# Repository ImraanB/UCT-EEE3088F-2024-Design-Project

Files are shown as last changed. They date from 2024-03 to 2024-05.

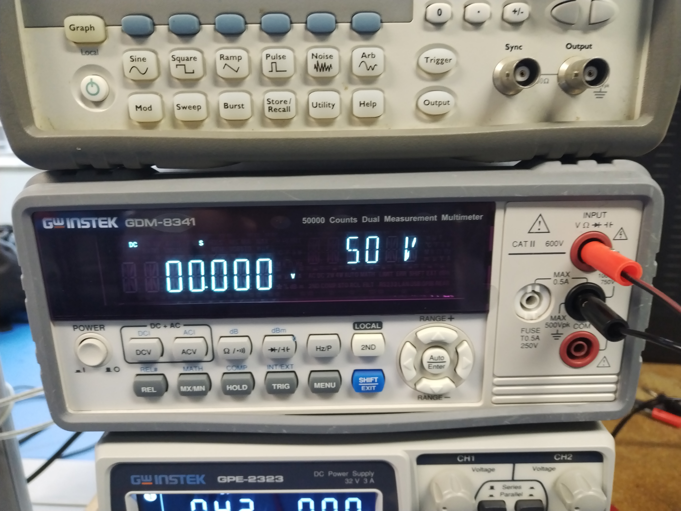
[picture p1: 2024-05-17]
Power subsystem/Testing/Testing pictures/IMG_20240510_095945.jpg

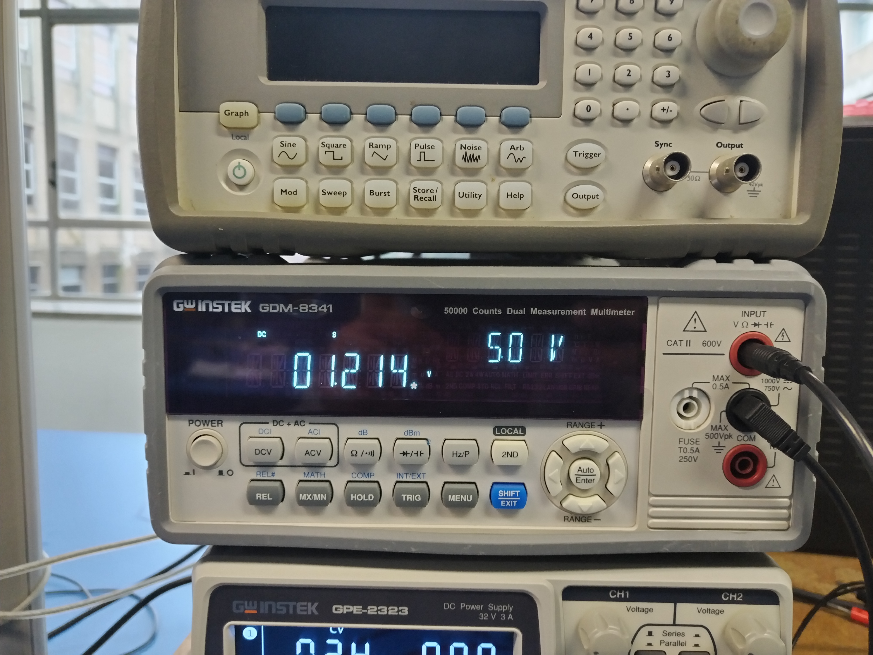
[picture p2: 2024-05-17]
Power subsystem/Testing/Testing pictures/adc voltage at 2v4.jpg

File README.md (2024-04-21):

# UCT-EEE3088F-2024-Design-Project
This is a repository for the UCT EEE3088F 2024 Micro-mouse Project
# Overall Project
This project involves designing a micromouse that will be able to move through a maze.
There are 4 subsystems that work together to form the micromouse:
## The motherboard
(We are given this) Connects all the PCBs together.
## The Processor
(We are given this) Contains an STM32L476 microcontroller. This microcontroller will be used to program different sections and subsystems of the micromouse.
## The Power
Responsible for powering the entire system:
- Run motors and charge battery
- Fit onto pin headers on motherboard
- It will need to be able to be an apporpriate size for balance and space issues
## The Sensor
Resposible for detecting/sensing objects
- Detect objects
- Fit onto pin headers on motherboard
- It will need to be able to be an apporpriate size for balance and space issues

# How this GitHub repo works
There are 2 main folders for the 2 subsystems that need to be designed: Power and Sensing.
Each of these folders contain the relevant documents that are associated with each subsystem

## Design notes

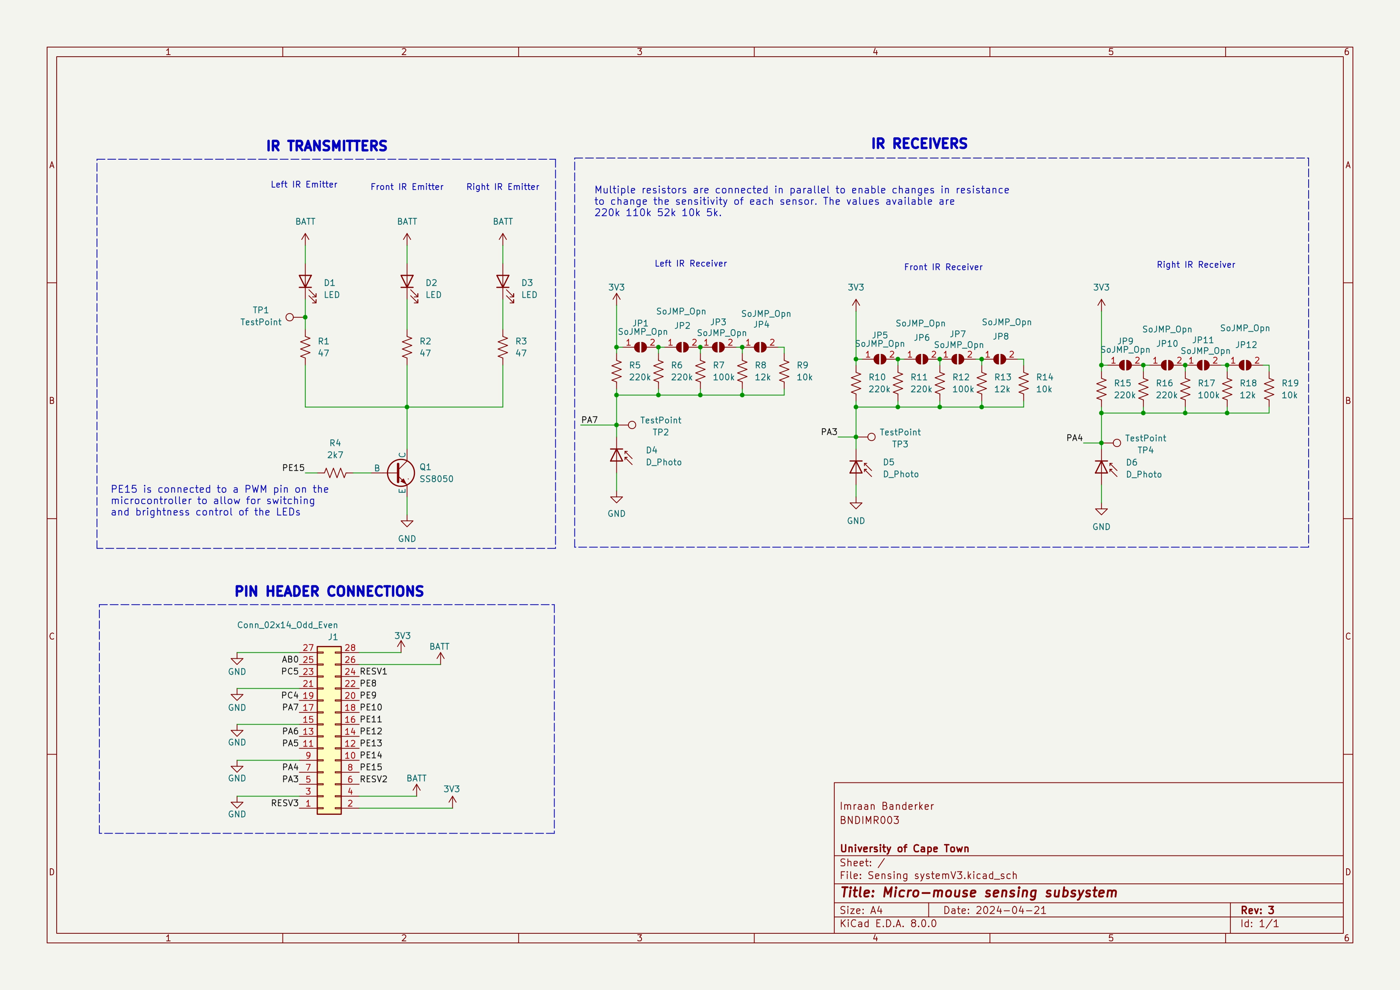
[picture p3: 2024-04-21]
Sensing subsystem/Images/Final Schematic.jpg

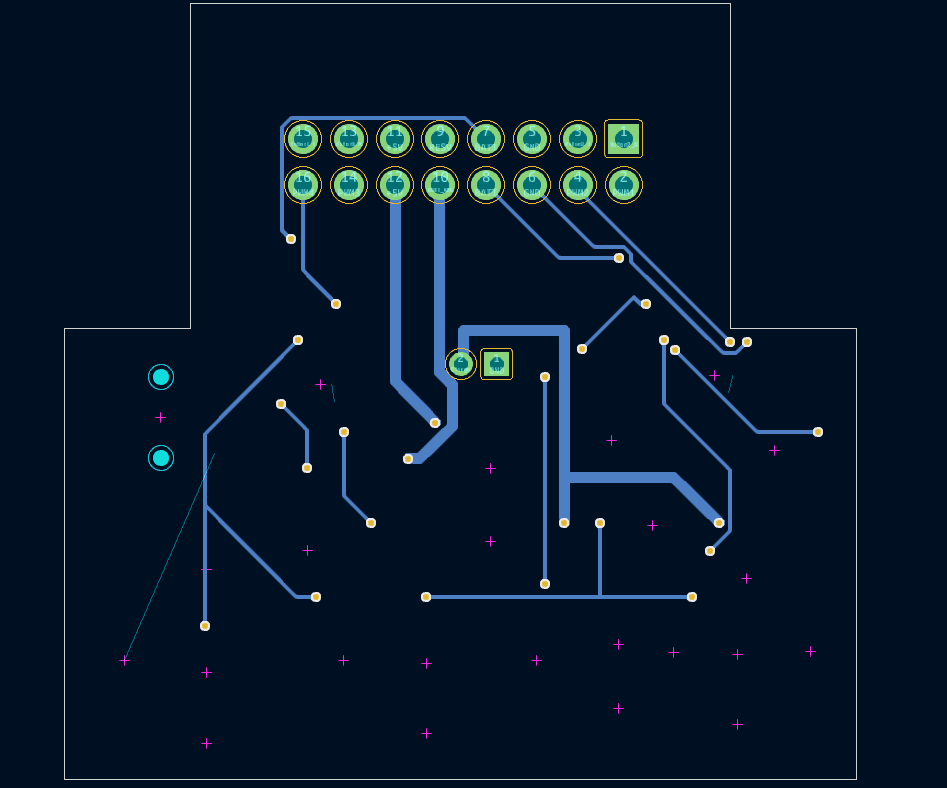
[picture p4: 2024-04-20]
Power subsystem/Design plan/Back PCB.png

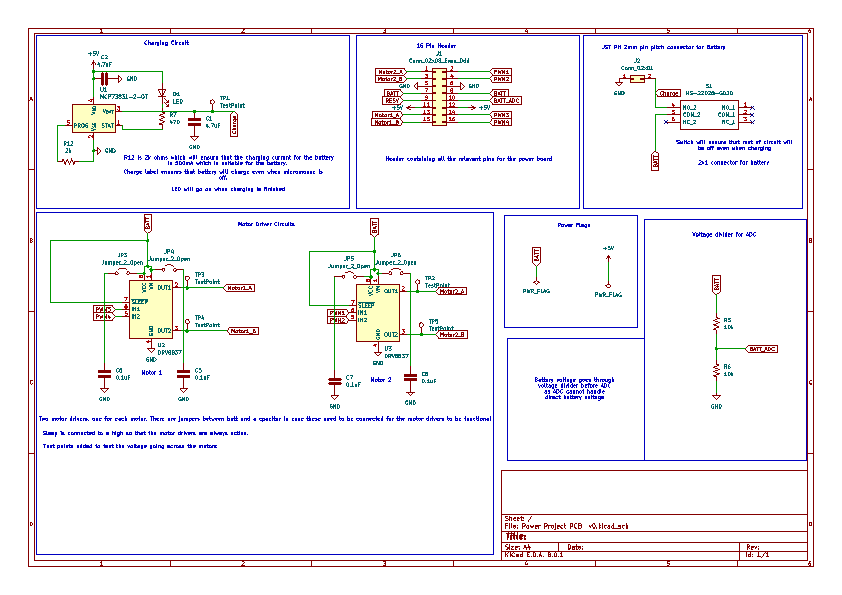
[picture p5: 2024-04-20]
Power subsystem/Design plan/Final Schematic.png

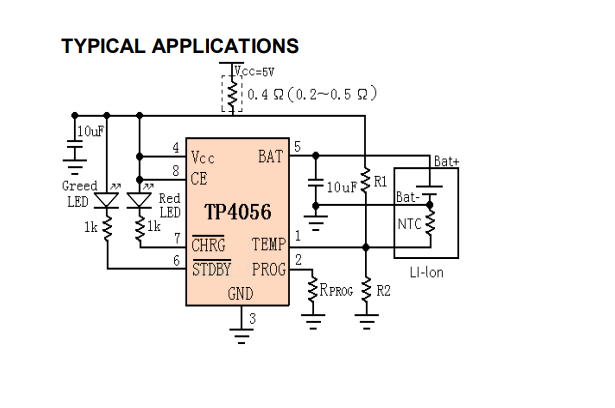
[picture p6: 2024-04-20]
Power subsystem/Design plan/TP4056 charging circuit.png

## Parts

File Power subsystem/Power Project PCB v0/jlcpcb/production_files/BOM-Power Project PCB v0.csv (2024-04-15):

Comment | Designator | Footprint | LCSC
10k | R5,R6 | R_0805_2012Metric | C17414
2k | R12 | R_0805_2012Metric | C17604
470 | R7 | R_0805_2012Metric | C17710
4.7uF | C1,C2,C5,C6,C7,C8 | C_0805_2012Metric | C1779
DRV8837 | U2,U3 | WSON-8-1EP_2x2mm_P0.5mm_EP0.9x1.6mm | C39159
MCP73831-2-OT | U1 | SOT-23-5 | C424093
LED | D1 | LED_0805_2012Metric | C84256
MS-22D28-G020 | S1 | MS22D28G020 | C963205

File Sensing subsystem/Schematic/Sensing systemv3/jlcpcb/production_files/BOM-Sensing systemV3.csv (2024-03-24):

Comment | Designator | Footprint | LCSC
100k | R12,R17,R7 | R_0805_2012Metric | C149504
10k | R14,R19,R9 | R_0805_2012Metric | C17414
12k | R13,R18,R8 | R_0805_2012Metric | C17444
2k7 | R4 | R_0805_2012Metric | C17530
220k | R10,R11,R15,R16,R5,R6 | R_0805_2012Metric | C17556
47 | R1,R2,R3 | R_0805_2012Metric | C17714
SS8050 | Q1 | SOT-23-3 | C2150
LED | D1,D2,D3 | LED_D5.0mm_Horizontal_O1.27mm_Z3.0mm_Clear | C405270
D_Photo | D4,D5,D6 | LED_D5.0mm_Horizontal_O1.27mm_Z3.0mm_Clear | C95399

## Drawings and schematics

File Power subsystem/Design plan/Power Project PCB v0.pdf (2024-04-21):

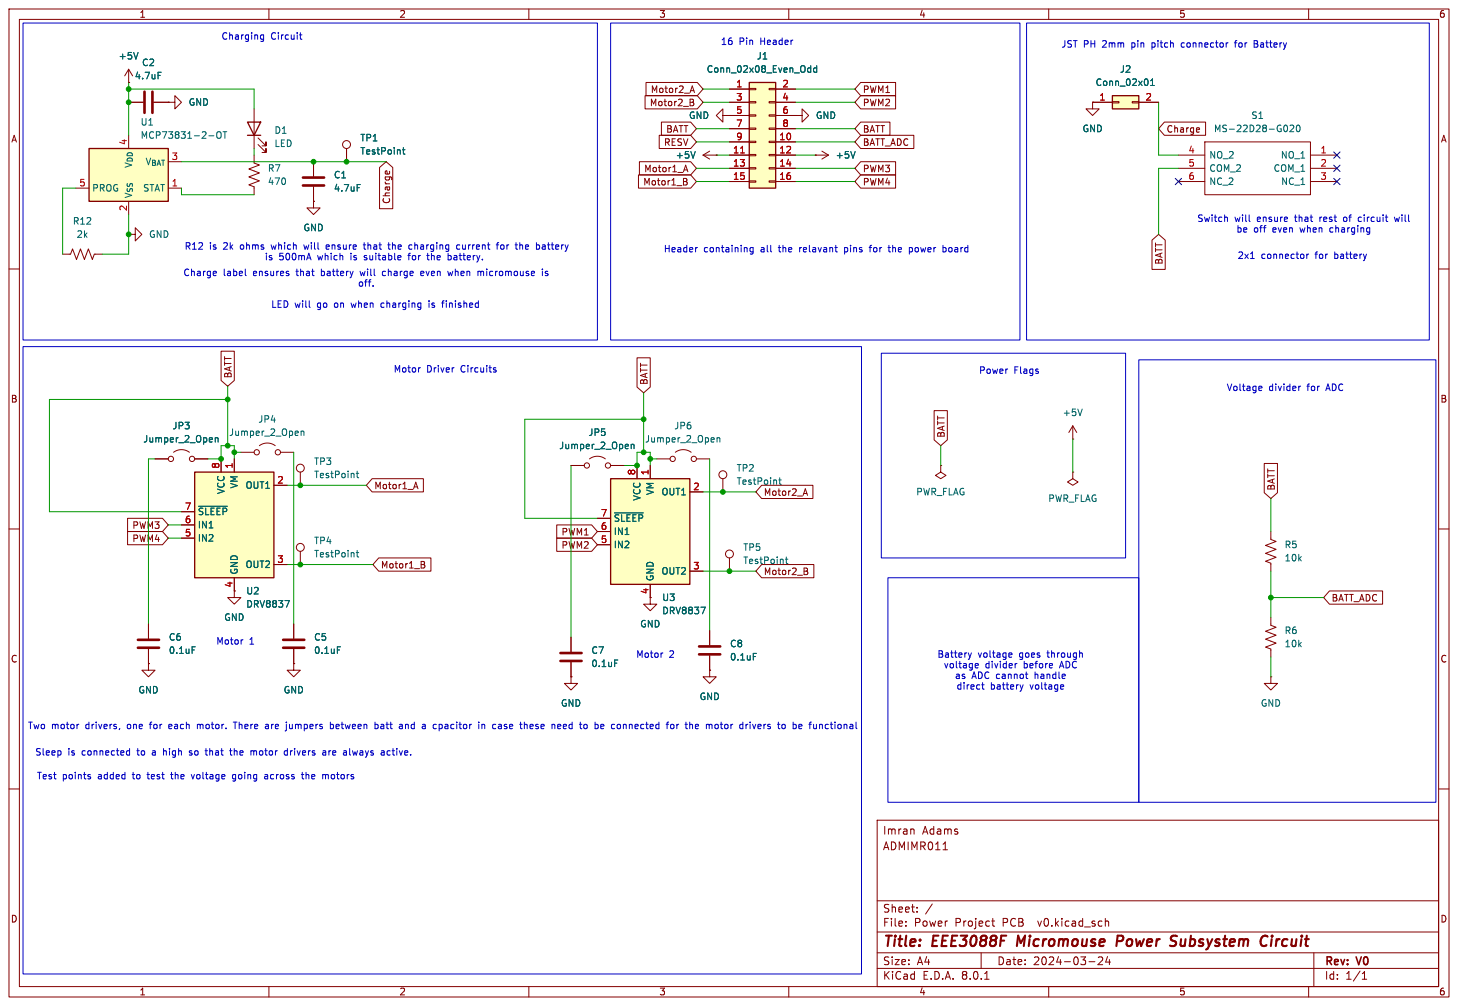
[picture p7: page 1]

Voltage divider for ADC

voltage divider before ADC
as ADC cannot handle

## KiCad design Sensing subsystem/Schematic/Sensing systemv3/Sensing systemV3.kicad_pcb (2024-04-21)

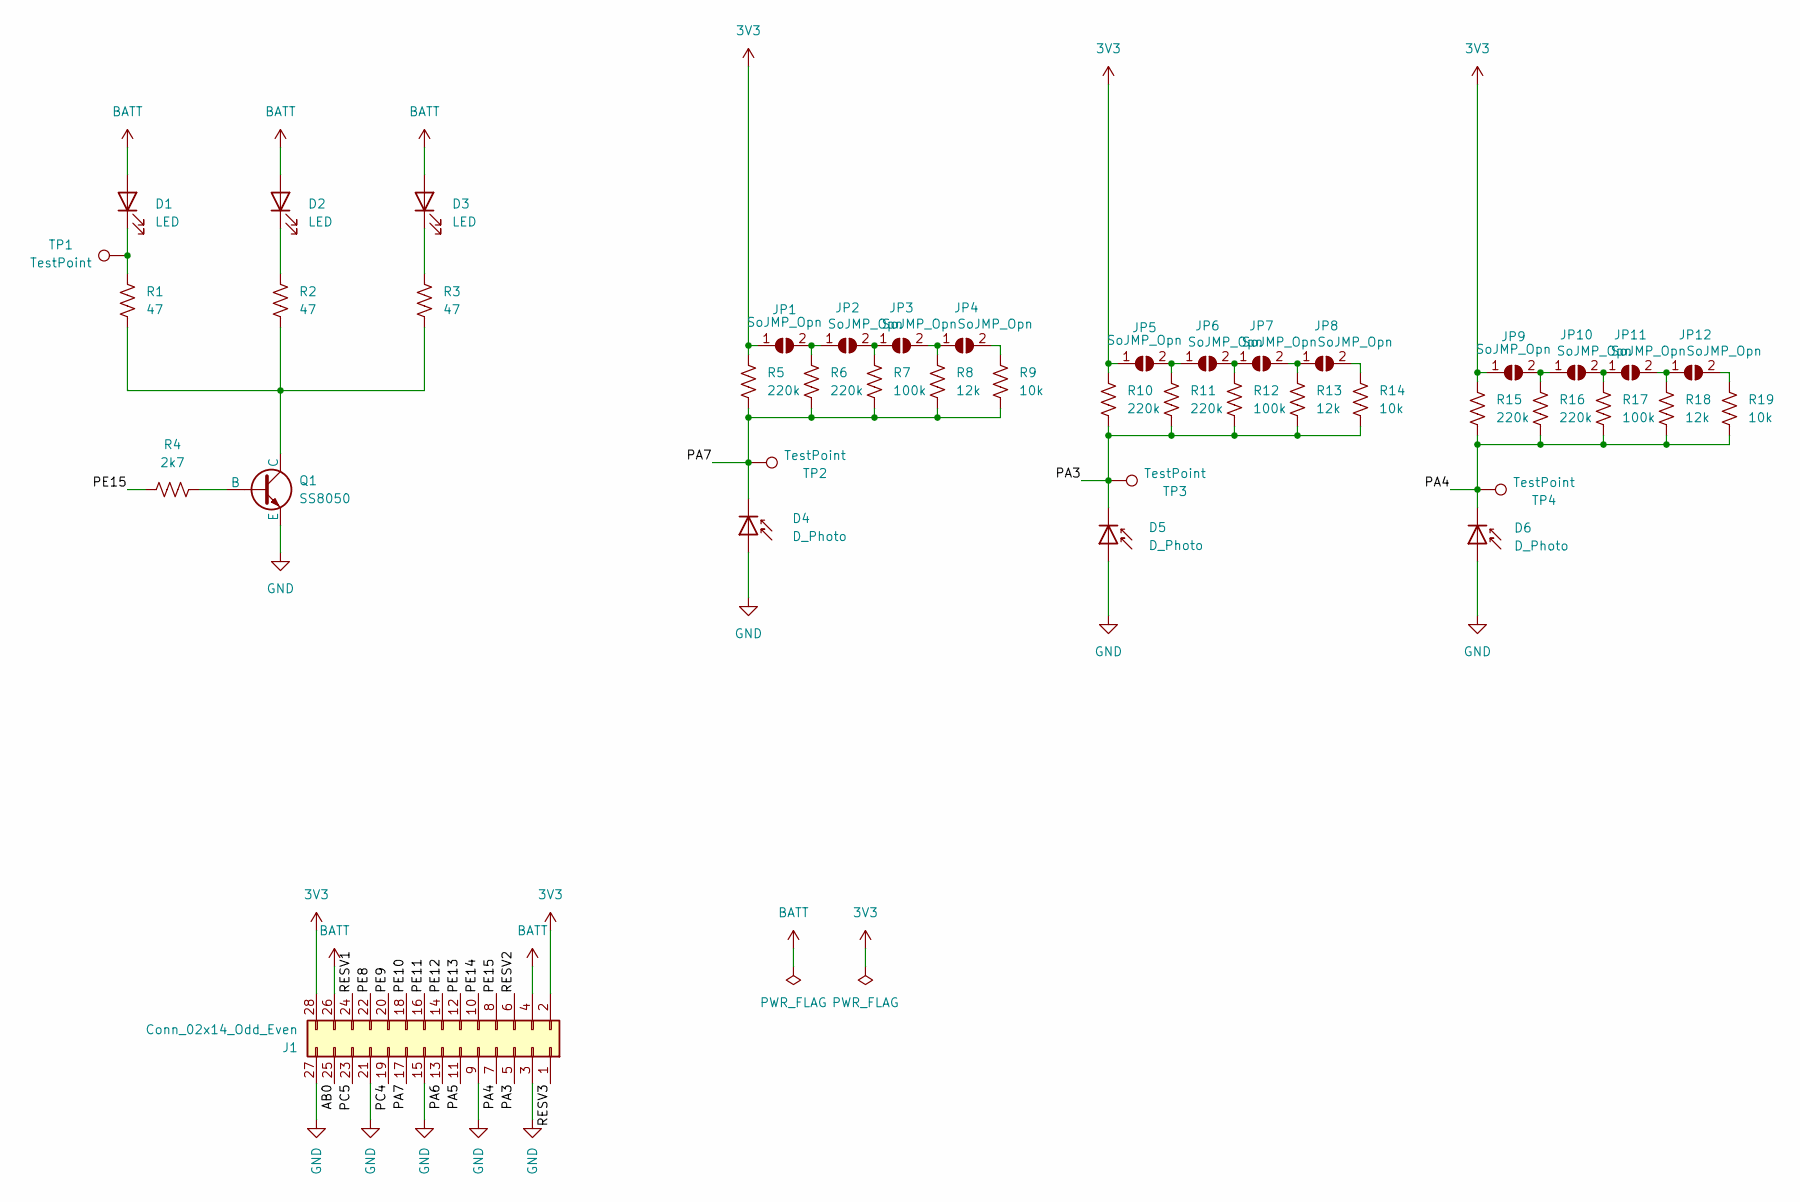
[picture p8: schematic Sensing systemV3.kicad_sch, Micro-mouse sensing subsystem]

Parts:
D1, D2, D3: LED; LED_D5.0mm_Horizontal_O1.27mm_Z3.0mm_Clear; LCSC C405270
D4, D5, D6: D_Photo; LED_D5.0mm_Horizontal_O1.27mm_Z3.0mm_Clear; LCSC C95399
J1: Conn_02x14_Odd_Even; PinHeader_2x14_P2.54mm_Vertical
JP1, JP2, JP3, JP4, JP5, JP6, JP7, JP8, JP9, JP10, JP11, JP12: SoJMP_Opn; SolderJumper-2_P1.3mm_Open_RoundedPad1.0x1.5mm
Q1: SS8050; SOT-23-3; LCSC C2150
R1, R2, R3: 47; R_0805_2012Metric; LCSC C17714
R4: 2k7; R_0805_2012Metric; LCSC C17530
R5, R6, R10, R11, R15, R16: 220k; R_0805_2012Metric; LCSC C17556
R7, R12, R17: 100k; R_0805_2012Metric; LCSC C149504
R8, R13, R18: 12k; R_0805_2012Metric; LCSC C17444
R9, R14, R19: 10k; R_0805_2012Metric; LCSC C17414
TP1, TP2, TP3, TP4: TestPoint; TestPoint_Pad_2.0x2.0mm

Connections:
3V3: J1.2, J1.28, JP1.1 (A), JP5.1 (A), JP9.1 (A), R5.1, R10.1, R15.1
/AB0: J1.25
/PA3: D5.1 (K), J1.5, R10.2, R11.2, R12.2, R13.2, R14.2, TP3.1
/PA4: D6.1 (K), J1.7, R15.2, R16.2, R17.2, R18.2, R19.2, TP4.1
/PA5: J1.11
/PA6: J1.13
/PA7: D4.1 (K), J1.17, R5.2, R6.2, R7.2, R8.2, R9.2, TP2.1
/PC4: J1.19
/PC5: J1.23
/PE8: J1.22
/PE9: J1.20
/PE10: J1.18
/PE11: J1.16
/PE12: J1.14
/PE13: J1.12
/PE14: J1.10
/PE15: J1.8, R4.1
/RESV1: J1.24
/RESV2: J1.6
/RESV3: J1.1
BATT: D1.2 (A), D2.2 (A), D3.2 (A), J1.4, J1.26
GND: D4.2 (A), D5.2 (A), D6.2 (A), J1.3, J1.9, J1.15, J1.21, J1.27, Q1.3 (E)
unnamed: D1.1 (K), R1.1, TP1.1
unnamed: D2.1 (K), R2.1
unnamed: D3.1 (K), R3.1
unnamed: JP1.2 (B), JP2.1 (A), R6.1
unnamed: JP2.2 (B), JP3.1 (A), R7.1
unnamed: JP3.2 (B), JP4.1 (A), R8.1
unnamed: JP4.2 (B), R9.1
unnamed: JP5.2 (B), JP6.1 (A), R11.1
unnamed: JP6.2 (B), JP7.1 (A), R12.1
unnamed: JP7.2 (B), JP8.1 (A), R13.1
unnamed: JP8.2 (B), R14.1
unnamed: JP9.2 (B), JP10.1 (A), R16.1
unnamed: JP10.2 (B), JP11.1 (A), R17.1
unnamed: JP11.2 (B), JP12.1 (A), R18.1
unnamed: JP12.2 (B), R19.1
unnamed: Q1.2 (B), R4.2
unnamed: Q1.1 (C), R1.2, R2.2, R3.2

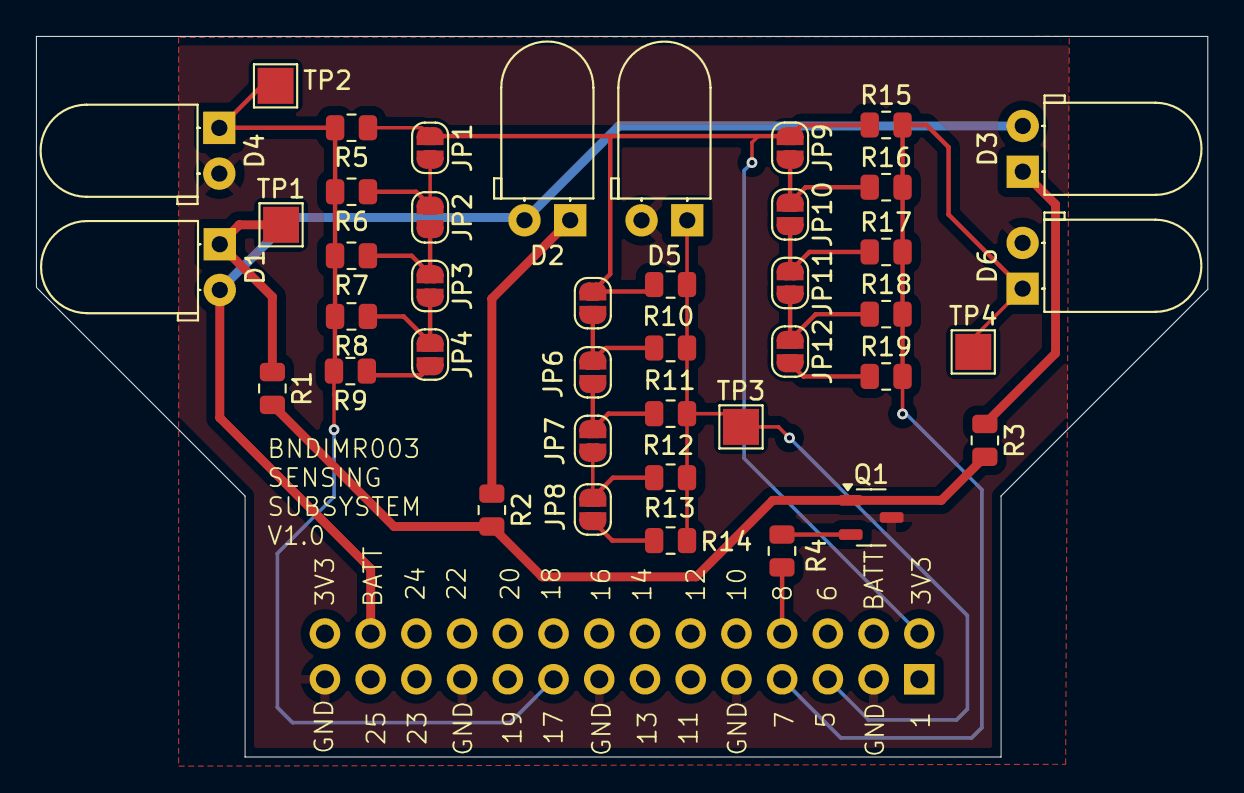
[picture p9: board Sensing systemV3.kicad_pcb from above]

Board: 2 copper layers, 65.1 x 40.0 mm, 43 parts (1 on the bottom side), 24 nets.

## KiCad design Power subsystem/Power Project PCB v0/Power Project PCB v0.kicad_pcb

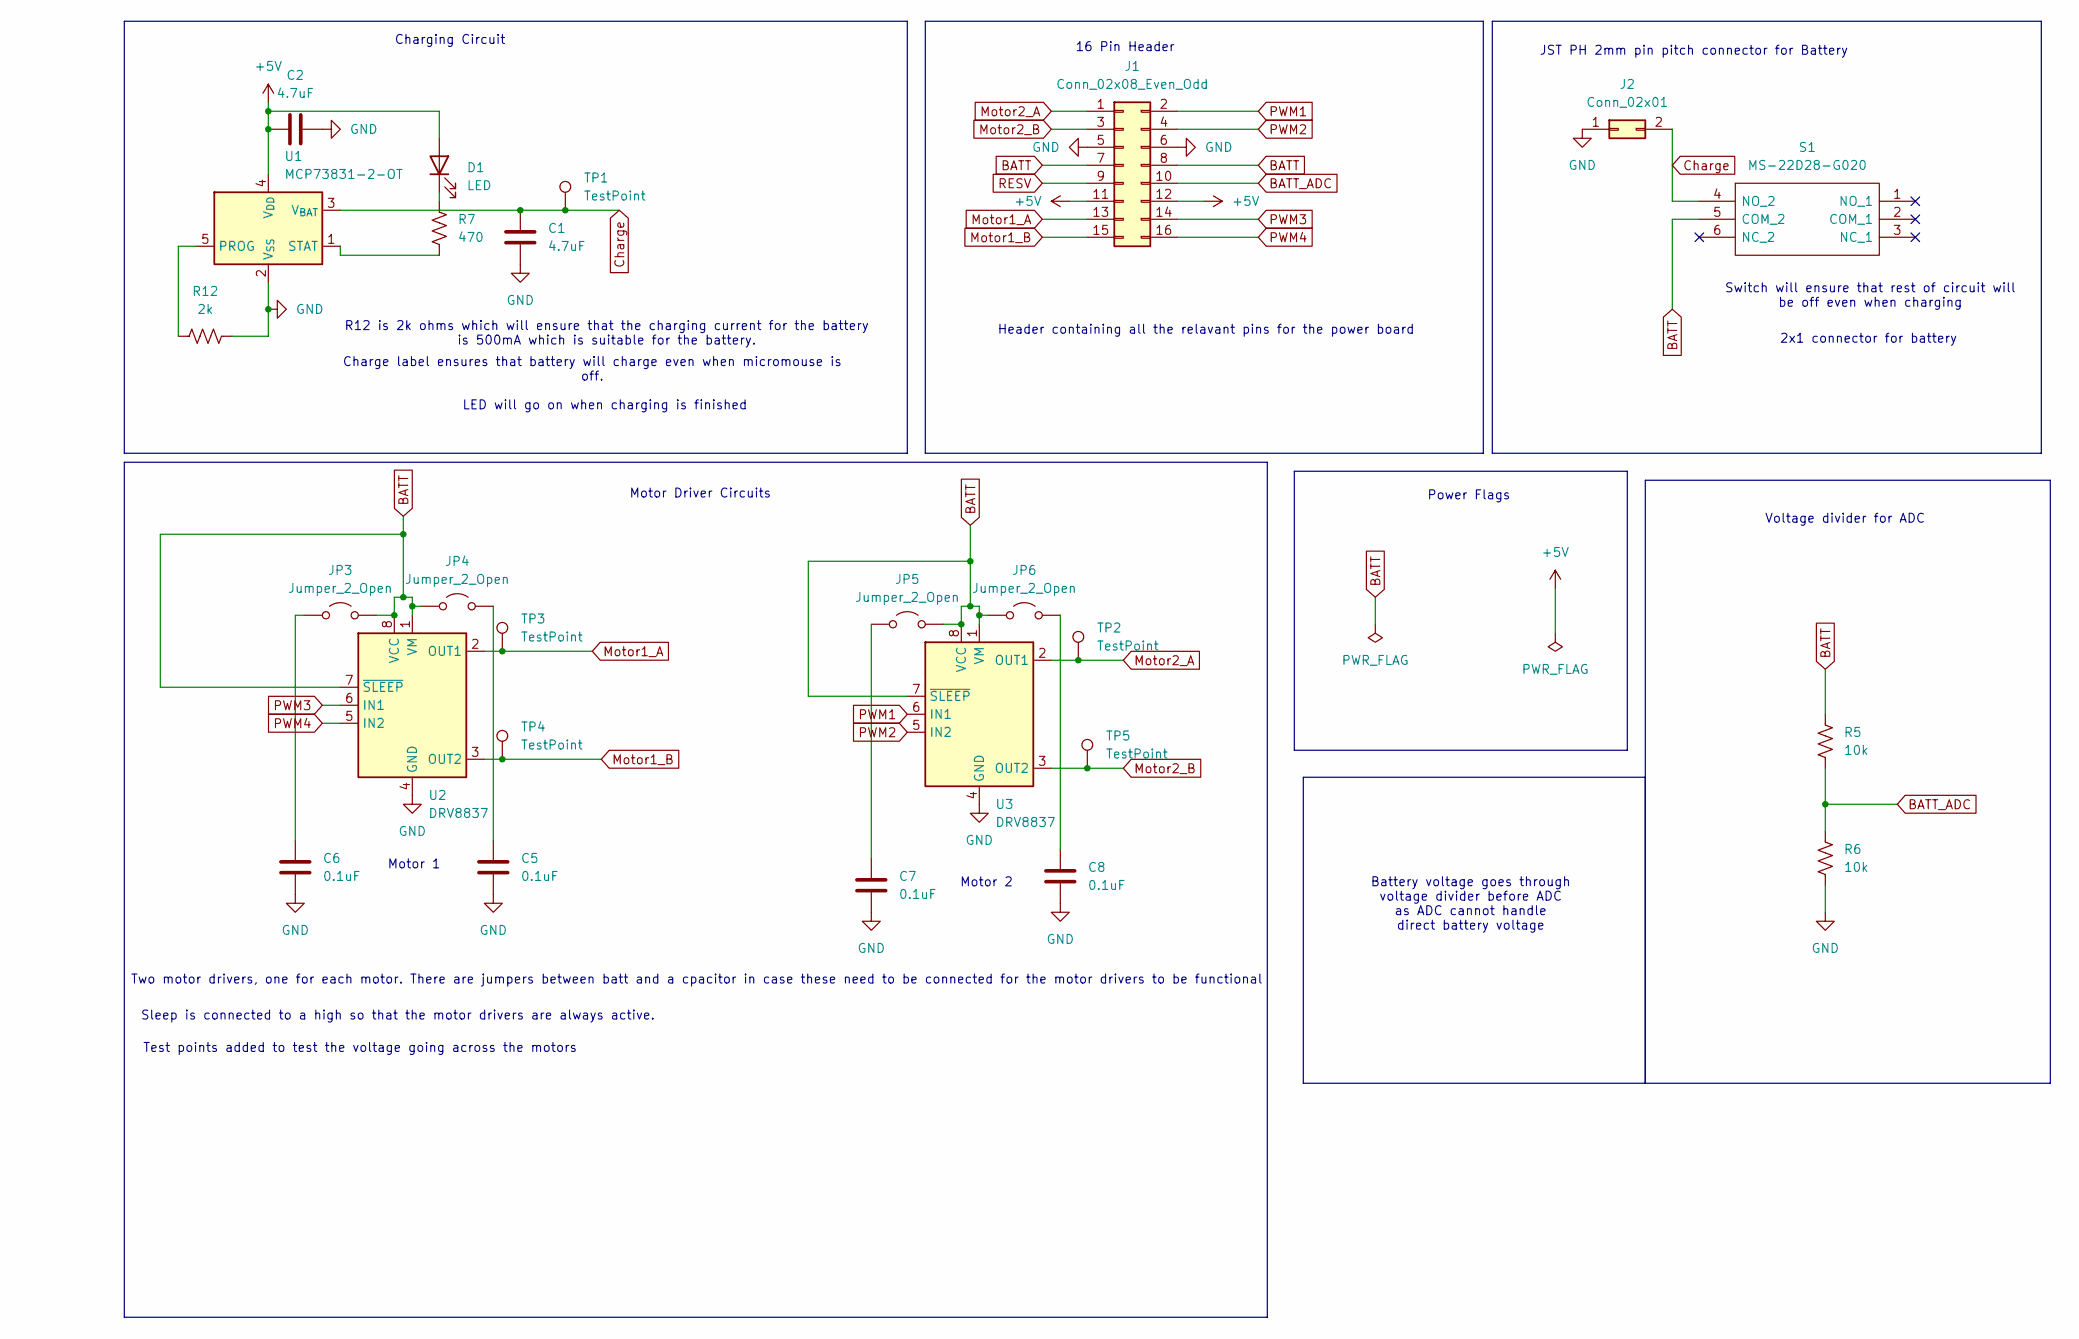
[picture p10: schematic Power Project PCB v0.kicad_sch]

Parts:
C1, C2: 4.7uF; C_0805_2012Metric; LCSC C1779
C5, C6, C7, C8: 0.1uF; C_0805_2012Metric; LCSC C1779
D1: LED; LED_0805_2012Metric; LCSC C84256
J1: Conn_02x08_Even_Odd; PinHeader_2x08_P2.54mm_Vertical
J2: Conn_02x01; PinHeader_2x01_P2.00mm_Vertical
JP3, JP4, JP5, JP6: Jumper_2_Open; SolderJumper-2_P1.3mm_Open_RoundedPad1.0x1.5mm
R5, R6: 10k; R_0805_2012Metric; LCSC C17414
R7: 470; R_0805_2012Metric; LCSC C17710
R12: 2k; R_0805_2012Metric; LCSC C17604
S1: MS-22D28-G020; MS22D28G020; Manufacturer_Part_Number MS-22D28-G020; LCSC C963205
TP1, TP2, TP3, TP4, TP5: TestPoint; TestPoint_Keystone_5019_Minature
U1: MCP73831-2-OT; SOT-23-5; LCSC C424093
U2, U3: DRV8837; WSON-8-1EP_2x2mm_P0.5mm_EP0.9x1.6mm; LCSC C39159

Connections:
+5V: C2.1, D1.2 (A), J1.11, J1.12, U1.4 (V_{DD})
BATT: J1.7, J1.8, JP3.2 (B), JP4.1 (A), JP5.2 (B), JP6.1 (A), R5.1, S1.5 (COM_2), U2.1 (VM), U2.7 (~SLEEP), U2.8 (VCC), U3.1 (VM), U3.7 (~SLEEP), U3.8 (VCC)
BATT_ADC: J1.10, R5.2, R6.1
Charge: C1.1, J2.2, S1.4 (NO_2), TP1.1, U1.3 (V_{BAT})
GND: C1.2, C2.2, C5.1, C6.1, C7.1, C8.1, J1.5, J1.6, J2.1, R6.2, R12.1, U1.2 (V_{SS}), U2.4 (GND), U2.9 (GND), U3.4 (GND), U3.9 (GND)
Motor1_A: J1.13, TP3.1, U2.2 (OUT1)
Motor1_B: J1.15, TP4.1, U2.3 (OUT2)
Motor2_A: J1.1, TP2.1, U3.2 (OUT1)
Motor2_B: J1.3, TP5.1, U3.3 (OUT2)
unnamed: D1.1 (K), R7.1
unnamed: C6.2, JP3.1 (A)
unnamed: C5.2, JP4.2 (B)
unnamed: C7.2, JP5.1 (A)
unnamed: C8.2, JP6.2 (B)
unnamed: R12.2, U1.5 (PROG)
unnamed: R7.2, U1.1 (STAT)
PWM1: J1.2, U3.6 (IN1)
PWM2: J1.4, U3.5 (IN2)
PWM3: J1.14, U2.6 (IN1)
PWM4: J1.16, U2.5 (IN2)
RESV: J1.9

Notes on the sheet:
Motor 1
Battery voltage goes through voltage divider before ADC as ADC cannot handle direct battery voltage
Switch will ensure that rest of circuit will be off even when charging
Header containing all the relavant pins for the power board
Charging Circuit
Charge label ensures that battery will charge even when micromouse is off.
Motor 2
Sleep is connected to a high so that the motor drivers are always active.
16 Pin Header
LED will go on when charging is finished
R12 is 2k ohms which will ensure that the charging current for the battery is 500mA which is suitable for the battery.
Test points added to test the voltage going across the motors
Two motor drivers, one for each motor. There are jumpers between batt and a cpacitor in case these need to be connected for the motor drivers to be functional
JST PH 2mm pin pitch connector for Battery
2x1 connector for battery
Motor Driver Circuits
Voltage divider for ADC
Power Flags

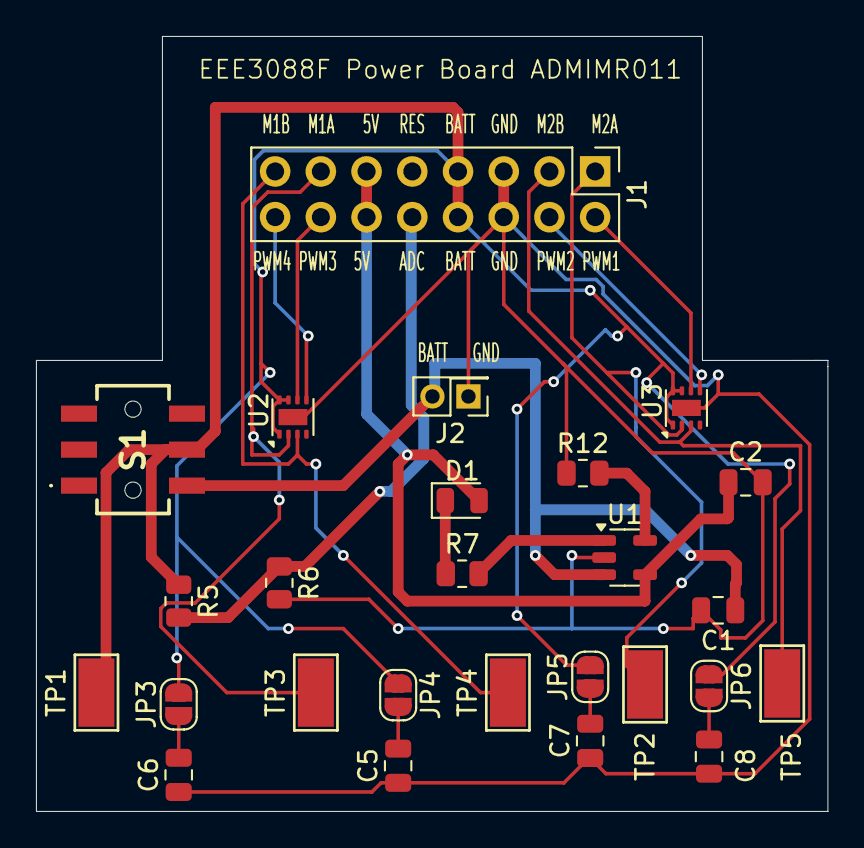
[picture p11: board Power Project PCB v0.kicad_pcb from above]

Board: 2 copper layers, 44.0 x 43.1 mm, 26 parts (0 on the bottom side), 20 nets.

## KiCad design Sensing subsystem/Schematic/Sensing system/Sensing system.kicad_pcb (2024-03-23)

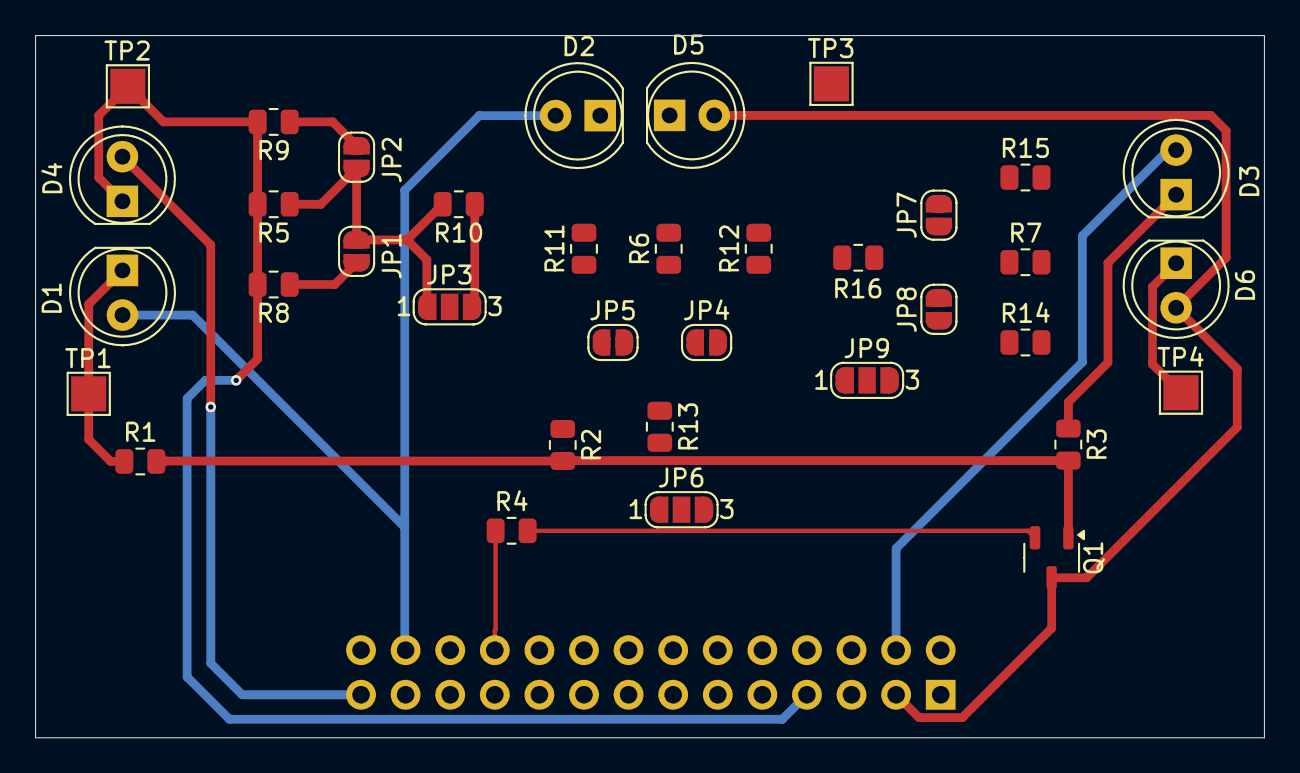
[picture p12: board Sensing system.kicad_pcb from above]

Board: 2 copper layers, 70.0 x 40.0 mm, 37 parts (1 on the bottom side), 24 nets.

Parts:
D1, D2, D3: LED; LED_D5.0mm
D4, D5, D6: D_Photo; LED_D5.0mm
J1: Conn_02x14_Odd_Even; PinHeader_2x14_P2.54mm_Vertical
JP1, JP2, JP4, JP5, JP7, JP8: SoJMP_Opn; SolderJumper-2_P1.3mm_Open_RoundedPad1.0x1.5mm
JP3, JP6, JP9: SoJMP_Opn3; SolderJumper-3_P1.3mm_Open_RoundedPad1.0x1.5mm_NumberLabels
Q1: SS8050; SOT-23-3
R1, R2, R3: 47; R_0805_2012Metric
R4: 2k7; R_0805_2012Metric
R5, R6, R7, R8, R9, R11, R12, R14, R15: 10k; R_0805_2012Metric
R10, R13, R16: 100k; R_0805_2012Metric
TP1, TP2, TP3, TP4: TestPoint; TestPoint_Pad_2.0x2.0mm

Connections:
3V3: J1.2, J1.28, JP3.2 (C), JP6.2 (C), JP9.2 (C)
/PA4: D4.1 (K), J1.7, R5.2, R8.2, R9.2, TP2.1
/PA5: D5.1 (K), J1.11, R6.2, R11.2, R12.2, TP3.1
/PA6: D6.1 (K), J1.13, R7.2, R14.2, R15.2, TP4.1
/PE8: J1.22, R4.1
BATT: D1.2 (A), D2.2 (A), D3.2 (A), J1.4, J1.26
GND: D4.2 (A), D5.2 (A), D6.2 (A), J1.3, J1.9, J1.15, J1.21, J1.27, Q1.3 (E)
unnamed: D1.1 (K), R1.1, TP1.1
unnamed: D2.1 (K), R2.1
unnamed: D3.1 (K), R3.1
unnamed: JP1.1 (A), R8.1
unnamed: JP1.2 (B), JP2.1 (A), JP3.1 (A), R5.1, R10.2
unnamed: JP2.2 (B), R9.1
unnamed: JP3.3 (B), R10.1
unnamed: JP4.1 (A), JP5.2 (B), JP6.1 (A), R6.1, R13.2
unnamed: JP4.2 (B), R12.1
unnamed: JP5.1 (A), R11.1
unnamed: JP6.3 (B), R13.1
unnamed: JP7.1 (A), JP8.2 (B), JP9.1 (A), R7.1, R16.2
unnamed: JP7.2 (B), R15.1
unnamed: JP8.1 (A), R14.1
unnamed: JP9.3 (B), R16.1
unnamed: Q1.2 (B), R4.2
unnamed: Q1.1 (C), R1.2, R2.2, R3.2

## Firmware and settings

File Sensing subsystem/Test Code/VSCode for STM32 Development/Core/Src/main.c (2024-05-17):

//********************************************************************
//*              EEE3088F sensing subsytem test code                 *
//*==================================================================*
//* WRITTEN BY: Jesse Arendse   	                 		         *
//* DATE CREATED: 07/04/2023                                         *
//* MODIFIED BY: Imraan Banderker                                    *
//* DATE MODIFIED: 07/05/2024                                        *
//*==================================================================*
//* PROGRAMMED IN: Visual Studio Code                                *
//* TARGET:        STM32F0                                           *
//*==================================================================*
//* DESCRIPTION: Test sensing functionality of the sensing module    *
//*                                                                  *
//********************************************************************
// INCLUDE FILES
//====================================================================
#include <stdio.h>
#include <stdbool.h>
#define STM32F051
#include <stm32f0xx.h>
#include <stm32f051x8.h>
#include "lcd_stm32f0.c"
//====================================================================
// GLOBAL CONSTANTS
//====================================================================

//====================================================================
// GLOBAL VARIABLES
//====================================================================
uint16_t ADC_value_left;
uint16_t ADC_value_front;
uint16_t ADC_value_right;

bool holdOnFront = true;    // true: IR remains on if front wall is present, false: IR always pulses 
bool steadyLED = true;          
// true: LEDs change state only when IR is present 
// false: LEDs turn off when IR light turns off

uint8_t displayADC = 6;         // choose to disply ADC value for: left=7 front=6 right=5 none=0
uint16_t frontThreshold = 2400;
uint16_t sideThreshold = 2400;

//====================================================================
// FUNCTION DECLARATIONS
//====================================================================
void init_GPIOA(void);
void init_GPIOB(void); 
void init_ADC(void); 
void adcLCDdisplay(uint16_t number);
void init_TIM14(void);
void TIM14_IRQHandler (void);
void leftLED(void);
void frontLED(void);
void rightLED(void);

//====================================================================
// MAIN FUNCTION
//====================================================================
int main(void) {
    init_GPIOA();
    init_GPIOB();
    init_ADC();
    init_LCD();
    init_TIM14();


    while(1) {
        /*
            read ADC for left sensor
        */
        ADC1->CHSELR  |=  ADC_CHSELR_CHSEL0;  // select ADC channel 0(for ADC_IN0 = PA0)
        ADC1->CR  |=  ADC_CR_ADSTART;  // start conversion
        while( (ADC1->ISR & ADC_ISR_EOC) == 0 );  // wait until conversion is complete
        ADC_value_left = ADC1->DR;
        ADC1->CHSELR  &= ~ADC_CHSELR_CHSEL0;  // deselect ADC channel 0
        if(displayADC==7){
            adcLCDdisplay(ADC_value_left);      // display conversion result on the LCD
        }
        if(steadyLED){
            leftLED();
        }else{
            if (ADC_value_left<sideThreshold){
                GPIOB -> ODR |= GPIO_ODR_7;     //turn PB7 led on

            }else{
                GPIOB -> ODR &= ~GPIO_ODR_7;    //turn PB7 led off
            }
        }
        
        /*
            read ADC for front sensor
        */
        ADC1->CHSELR  |=  ADC_CHSELR_CHSEL1;  // select ADC channel 1(for ADC_IN1 = PA1)
        ADC1->CR  |=  ADC_CR_ADSTART;  // start conversion
        while( (ADC1->ISR & ADC_ISR_EOC) == 0 );  // wait until conversion is complete
        ADC_value_front = ADC1->DR;
        ADC1->CHSELR  &= ~ADC_CHSELR_CHSEL1; // deselect ADC channel 1

        if(displayADC==6){
            adcLCDdisplay(ADC_value_front);      // display conversion result on the LCD
        }

        if(steadyLED){
            frontLED();
        }else{
            if (ADC_value_front < frontThreshold){
                GPIOB -> ODR |= GPIO_ODR_6;     //turn PB6 led on
                if(holdOnFront){TIM14 -> CR1 &= ~TIM_CR1_CEN;}    // stop counter for TIM14

            }else{
                GPIOB -> ODR &= ~GPIO_ODR_6;    //turn PB6 led off
                if(holdOnFront){TIM14 -> CR1 |= TIM_CR1_CEN;}     //start counter for TIM14
            }
        }

        /*
            read ADC for right sensor
        */
        ADC1->CHSELR  |=  ADC_CHSELR_CHSEL2;  // select ADC channel 2(for ADC_IN2 = PA2)
        ADC1->CR  |=  ADC_CR_ADSTART;  // start conversion
        while( (ADC1->ISR & ADC_ISR_EOC) == 0 );  // wait until conversion is complete
        ADC_value_right = ADC1->DR;
        ADC1->CHSELR  &= ~ADC_CHSELR_CHSEL2; // deselect ADC channel 2

        if(displayADC==5){
            adcLCDdisplay(ADC_value_right);      // display conversion result on the LCD
        }

        if(steadyLED){
            rightLED();
        }else{
            if (ADC_value_right < sideThreshold){
                GPIOB -> ODR |= GPIO_ODR_5;     //turn PB5 led on

            }else{
                GPIOB -> ODR &= ~GPIO_ODR_5;    //turn PB5 led off
            }
        }
               
    }
} 

//====================================================================
// FUNCTION DEFINITIONS
//====================================================================
void init_GPIOA(void) { 
    RCC -> AHBENR |= RCC_AHBENR_GPIOAEN; // enable clock signal to Port A
    GPIOA -> MODER |= GPIO_MODER_MODER0;  // configure pin PA0 to analog input mode
    GPIOA -> MODER |= GPIO_MODER_MODER1;  // configure pin PA1 to analog input mode
    GPIOA -> MODER |= GPIO_MODER_MODER2;  // configure pin PA2 to analog input mode
    GPIOA -> MODER |= GPIO_MODER_MODER3_0;  // configure pin PA3 to output mode

} 

void init_GPIOB(void){
    RCC -> AHBENR |= RCC_AHBENR_GPIOBEN; // enable clock to GPIOB
    GPIOB -> MODER |= GPIO_MODER_MODER5_0;  // set PB5 to output mode
    GPIOB -> MODER |= GPIO_MODER_MODER6_0;  // set PB6 to output mode
    GPIOB -> MODER |= GPIO_MODER_MODER7_0;  // set PB7 to output mode

    GPIOB -> MODER |= GPIO_MODER_MODER10_0;  // set PB10 to output mode

    GPIOB -> ODR &= ~GPIO_ODR_5;
    GPIOB -> ODR &= ~GPIO_ODR_6;
    GPIOB -> ODR &= ~GPIO_ODR_7;
    GPIOB -> ODR &= ~GPIO_ODR_10;
    
}

void init_ADC(void) { 
    ADC1->CR &= ~ADC_CR_ADEN;  // ensure ADC is disabled before calibration
    ADC1->CR |= ADC_CR_ADCAL;  // initiate ADC calibration

    RCC->APB2ENR  |=  RCC_APB2ENR_ADCEN;  // connect ADC to APB clock

    ADC1->CFGR1  |= 0b0000;  // configure ADC to res of 12bits
    ADC1->CFGR1  &= ~ADC_CFGR1_CONT;  // set to single conversion mode

    ADC1->CR  |=  ADC_CR_ADEN;  // enable ADC           
    while ( (ADC1->ISR & ADC_ISR_ADRDY) == 0 ){ }  // exit when ADC has stabilizeD
}

void adcLCDdisplay(uint16_t number) {
    /* for 12bit res, we expect a decimal number of up to fourdigits */
    uint8_t first_digit = number/1000; 
    uint8_t second_digit = (number - first_digit*1000)/100;
    uint8_t third_digit = (number - second_digit*100 - first_digit*1000)/10;
    uint8_t fourth_digit = number - third_digit*10 -second_digit*100 - first_digit*1000;
    
    lcd_command(CURSOR_HOME);  // reset cursor to home 
    lcd_putchar(first_digit+'0');
    lcd_putchar(second_digit+'0');
    lcd_putchar(third_digit+'0');
    lcd_putchar(fourth_digit+'0');
    
    }



void init_TIM14 (void){
    RCC -> APB1ENR |= RCC_APB1ENR_TIM14EN; // enable the clock
    TIM14 -> PSC = 122;                   //  If CLK = 8MHz, then Tov = 1s 
    TIM14 -> ARR = 65040;               // If CLK = 8MHz, then Tov = 1s
    TIM14 -> DIER |= TIM_DIER_UIE;    //  enable Timer 14 interrupt
    NVIC_EnableIRQ(TIM14_IRQn);     // unmask the TIM14 interrupt in the NVIC
    TIM14 -> CR1 |= TIM_CR1_CEN;    //  start counter for Timer 14     
}

void TIM14_IRQHandler (void){
    if ((GPIOB->ODR & GPIO_ODR_10) ==0){
        GPIOA -> ODR |= GPIO_ODR_3;     // turn IRs on
        GPIOB -> ODR |= GPIO_ODR_10;     //turn led on

    }else{
        GPIOA -> ODR &= ~GPIO_ODR_3;      // turn IRs off
        GPIOB -> ODR &= ~GPIO_ODR_10;    //turn led off
    } 
    TIM14 -> SR &= ~TIM_SR_UIF;  // clears the interrupt flag   
}

void leftLED(void){
        if (GPIOB -> ODR & GPIO_ODR_10){
            if (ADC_value_left < sideThreshold){
                GPIOB -> ODR |= GPIO_ODR_7;     //turn PB7 led on

            }else{
                GPIOB -> ODR &= ~GPIO_ODR_7;    //turn PB7 led off
            }   
        }
}

void frontLED(void){
        if (GPIOB -> ODR & GPIO_ODR_10){
            if (ADC_value_front < frontThreshold){
                GPIOB -> ODR |= GPIO_ODR_6;     //turn PB6 led on
                if(holdOnFront){TIM14 -> CR1 &= ~TIM_CR1_CEN;}    // stop counter for TIM14

            }else{
                GPIOB -> ODR &= ~GPIO_ODR_6;    //turn PB6 led off
                if(holdOnFront){TIM14 -> CR1 |= TIM_CR1_CEN;}    //start counter for TIM14
            }   
        }
}
void rightLED(void){
        if (GPIOB -> ODR & GPIO_ODR_10){
            if (ADC_value_right < sideThreshold){
                GPIOB -> ODR |= GPIO_ODR_5;     //turn PB5 led on

            }else{
                GPIOB -> ODR &= ~GPIO_ODR_5;    //turn PB5 led off
            }   
        }
}



//********************************************************************
// END OF PROGRAM
//********************************************************************

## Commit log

2024-03-17 Add files via upload
    Data Sheet for Battery Charge controller
2024-03-24 Sensing system
    [BOM-Sensing systemV3.csv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]
2024-04-15 PCB and schematic kicad files
    [BOM-Power Project PCB v0.csv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]
2024-04-17 Create ~Power Project PCB v0.kicad_sch.lck
2024-04-17 Create battery charging circuit .png
2024-04-21 Create 3d pcb.png
